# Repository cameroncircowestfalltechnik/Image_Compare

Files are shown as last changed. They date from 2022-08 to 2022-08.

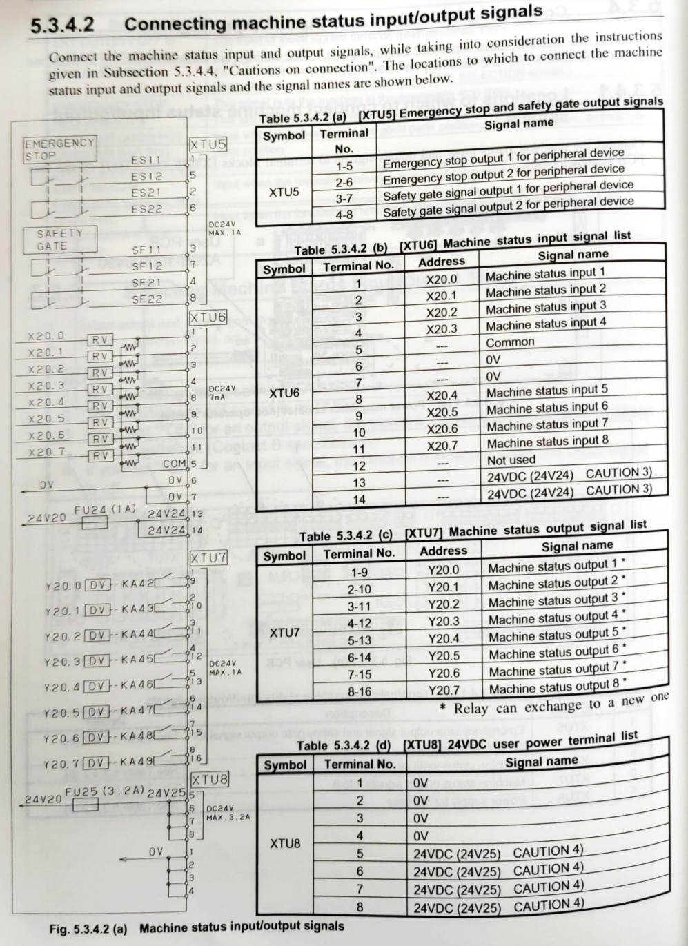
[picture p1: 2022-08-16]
Documentation/Wiring Terminals.png

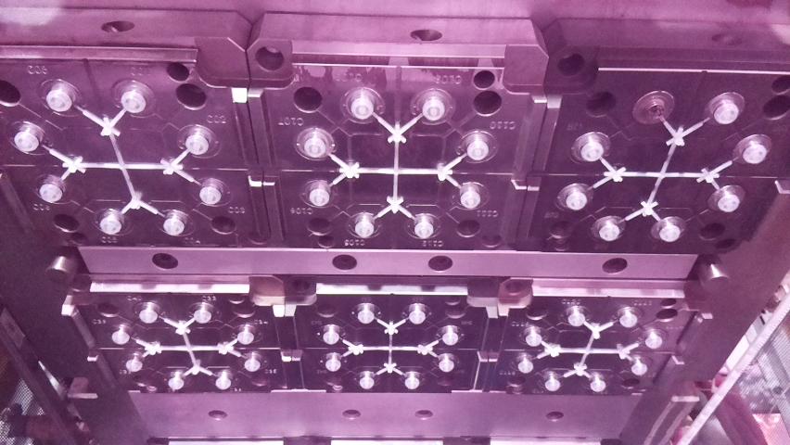
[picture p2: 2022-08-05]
Main/comparison_images/compare_full_ctrl.jpg

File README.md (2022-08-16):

# Main.py is currently the most up to date version!
# Image_Compare
This is yet another look at the current state of the project. Below I will go over each file in the repo. This time around the system contains two Raspberry Pi's a client attached to the machine that is able to operate independently and a server that is currently just used for data archival.

# Scripts
### Main.py
This is the main program of the current config and lives on the client. It has two "daughter" programs that allow it to transmit to the server and restart properly but we'll go through those a little later.  
The general flow of the program is the following:  
-Startup and pull settings from config txt and write to the startup log  
-Calculate the max possible score to be able to classify misfires  
-startup the camera and wait for the input signals  
  -On mold open it collects an image of a mold full of parts then processes/analyzes it  
  -After eject fire it waits a moment and then takes a picture of the empty mold then processes/analyzes it  
  -Interprets the processing output and decides to either throw the alarm or not  
-Simultaneously it maintins a GUI capable of the following:  
  -Changing the camera/analysis settings behind a password protected window  
  -Save the settings to the config file  
  -Genearate an image mask to specify regions to check for discrepencies  
  -See help on how to operate the system  
  -Grant alarm access  
  -Transmit files  
  -Reset the password  
  -Open/close a touchscreen keyboard ([See this tutorial for setup](https://ozzmaker.com/virtual-keyboard-for-the-raspberry-pi/))  
  -View and reset both control images  
 I recommend going through the code line by line for exact detail as I commented just about every line

### Dev_old.py
This is a depreceated version of Main that moved most of the settings buttons to the main GUI page, this made debugging much easier as they buttons were not on their own password protected window.  

### Main_B.py
This is a variant of the main program designed to be deployed on a different setup. The main changes are that it is designed to maintaina single image, used larger images and process more efficiently. This is described in detail below:  
-Only processes masked areas at the cost of forcing masked area to be rectangular  
-Uses opencv contour detection to detect the areas defined by masking tool  
-Captures 1920x1080 images by default and then downscales them in all the GUI elements in order to display properly  

### Main_Startup.py
 This program allows the main script to restart itself. I encountered an issue where the program could start a new iteration of itself but would never close the old one. This would lead to a memory leak. As such this program is designed to attempt to close the main program and then launches it. Finally, the main program attempts to stop this program on its startup. This program is intended to be run on client startup.  

### Main_Transmit.py
This program is designed to transmit the the log files and output images to the server via SCP. From there it deletes the output images to save storage on the client. Additionally, this script is designed to wait for a receipt from the server or will timeout after a designated time as to designate to the operator whether or not files have been recieved by the server. This can also accept a couple arguments. Argument one is an optional argument to override the default server ip. Argument two is an optional argument to make the transmission status display via popups. Seeing as this script will run autonomously via scheduling but must also be able to run via user input it is important to give the user feedback with popups but not spam the screen with popups when run automatically. This script lives on the client.   

### Main_Recieve.py
This program is hosted on the server and checks for the reception of the client receipt. Upon its arrival it checks the receipt for the incoming image folder size as well as client IP. From there it waits for the image folder it is recieveing to be the same size as designated by the receipt. Once the whole folder is transfered, this script sends the server receipt. From here the script moves the files to the archive for the current day of the week. The archive in this case is a usb flash drive that can simply de disconnected to view data. Additionally if the usb drive is not foubd it will backup locally. This program is intended to be run on startup of the server.  

### Wiring_Check.py  
This program is meant to check the wiring of the relay and test the I/O. It presents a window that allows you to send the alarm and reset signals and displays the mold open and ejector fire signals. Additionally it writes the input signals to the termianl with a timestamp for more detail.  

# Files   
### server_receipt.csv
This is the receipt the server sends to the client. It has no contents and more or less acts as a way for the transmit script to check for a file sent from the server. This could be a good way for the server to send back some info similar to the client receipt discussed below.  
### start.desktop
I followed [this tutorial](https://learn.sparkfun.com/tutorials/how-to-run-a-raspberry-pi-program-on-startup/method-2-autostart) on setting up programs to run on boot with a GUI. Currently, in my system, its destination folder is /home/pi/.config/autostart. On the pi the file is called "prog" not "start" but this is likely a difference in raspbian vs windows choosing how to display as "prog" is defined in the contents of the file. In the current setup in just launches predeployment_copy.py but in the main deployment will run Main_Emulated_Startup.py. A similar setup of this is used to run Main_Recieve.py on startup of the server.  
### run.desktop  
I followed [this tutorial](https://www.hackster.io/kamal-khan/desktop-shortcut-for-python-script-on-raspberry-pi-fd1c63) on setting up executables for programs. This is meant to live on the desktop screen and acts as a shortcut to startup Main.py if operators accidentally close the program. I recommend enabling "Don't ask options on launch executable file" under Edit->Prefrences->General in the raspbian file explorer to execute this more seamlessly.  

# Main folder
This is a sample of the filesystem client programs use. It shows some samples of outputs as well as demonstrates the layout of the file system.  
### client_receipt.csv
This is the csv file sent by Main_Emulated_Transmit.py to the server to tell it the file size and client ip. Additionally the server checks for this file to confirm it is recieveing files. Line one contains the image folder size in bytes, line two contains the client ip.  
###  log.csv
This is the main log that tracks the decision making of Main.py every time it does processing. This formatted as to be self explanitory. As you can see logs contain the timestamp which doubles as the output image title, the score the image recieved, and whether or not it set off the alarm.  
### log_template.csv  
This is a copy of the log but with no data present. It is used by transmit to wipe the log file. This is done by copying this file over the log and naming it log.  
### startup_log.csv
This log is written to once on every startup, it tracks the startup time and settings upon startup. This one is also formatted to it should be pretty self explanitory when viewed in github.  
### config.txt
This is a sample of my current config file. It stores the following in this order, password, ISO, shutter speed, camera mode, image width, image height, image rotation, image detection threshold, sensitivity, mold open delay, ejector fire delay, machine name, and alarm access. 
### menu_image.jpg
This is a sample image that is used as the first image to be displayed when the client programs are launched. It stands as a placeholder until the program processes and displays a new image.  
### mask_preview.jpg  
This an image of the full control with the mask overlayed on top of it. It is intended to be part of the archive and allows the user to have a visual representation fo exactly what parts of the mold are being examined at the time of archival. This image is updated on startup and everytime a new mask is generated.  
### images folder
This is where the outpput images go to be stored and then sent to the server.  
### comparison_images folder
This is the folder in which the sample and control images are stored while the client programs run as well as the image mask.
### fail folder  
This folder contains a set of images for every failure/time the alarm is triggered. Upon an image not passing it saves the current raw input, the processed output, and the control image it is being compared against. This is intended to gice the user plenty of data for analyzing failed images.  

# archive Folder
This is a sample layout of the archive stored on the server desktop and USB drive. It is meant to be copied to theses locations for easy setup. Ignore/delete the files name placeholder, they are present to force githb to keep the folder.  

# Misc/Common Bugs/Setup
### SCP Setup
When setting up SCP file transfer (especially when scheduled via crontab) it is imprtant that the root user also has the credentials for scp transfer. This can be done by following [this tutorial](https://raspberrypi.stackexchange.com/questions/51877/will-an-automated-scp-script-share-files-between-pis-without-passwords/53214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) and then configuring it to be run by root by following [these instructions](https://raspberrypi.stackexchange.com/a/121742) in which you first generate a keyset, copy them between machines and then copy the keyset to be accessed by root. In a couple cases I had to manually make the /root/.ssh folder first.  
### Crontab Setup
I added the following lines to crontab to autorun some things (to make it run correctly setup with the command "sudo crontab -e".  
I added the following line to the client:  
`00 00 * * * /sbin/shutdown -r now` This restarts the system at midnight everyday.  
`05 00 * * * /usr/bin/python3 /home/pi/Desktop/Main_Transmit.py >> /home/pi/logs/Transmit.log 2>&1` This runs Main_Transmit.py everyday at 12:05 am and writes to a log at the specified location for debugging (this will be removed in final deployment).  
I added the following to the server:  
`00 00 * * * /sbin/shutdown -r now` This restarts the system at midnight everyday.  
`@reboot /usr/bin/python3 /home/pi/Desktop/Main_Recieve.py >> /home/pi/Desktop/log.log 2>&1` This runs the file recieve script on boot
### Documentation
This folder contains important files relating to the documentation of the project.
CAD: This folder contains all CAD files relating to the construction of the project. Everything designed to be 3d printed also has an stl.  
BOM.xlsx: This is a spreadsheet of the bill of materials to completely replicate the system
Setup tutorial.docx: This is a word document describing how to setup the system.
Wiring Diagram.png: This is an illustration of the wiring required to setup the system.

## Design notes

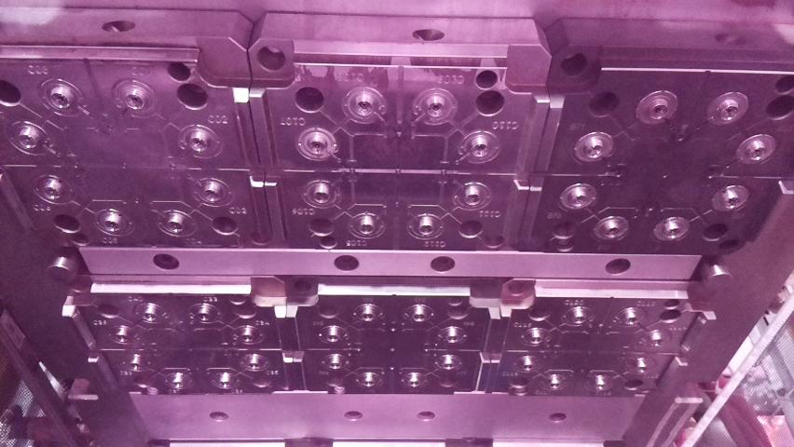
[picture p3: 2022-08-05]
Main/comparison_images/compare_empty_ctrl.jpg

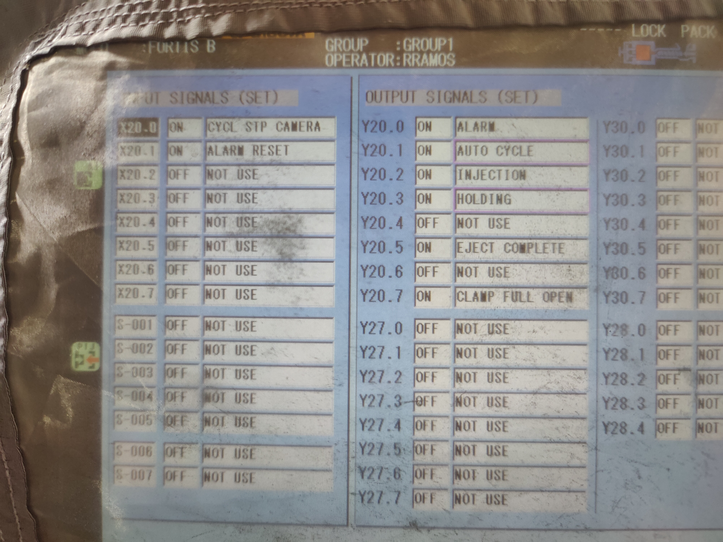
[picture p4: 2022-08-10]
Documentation/Machine IO Config.jpg

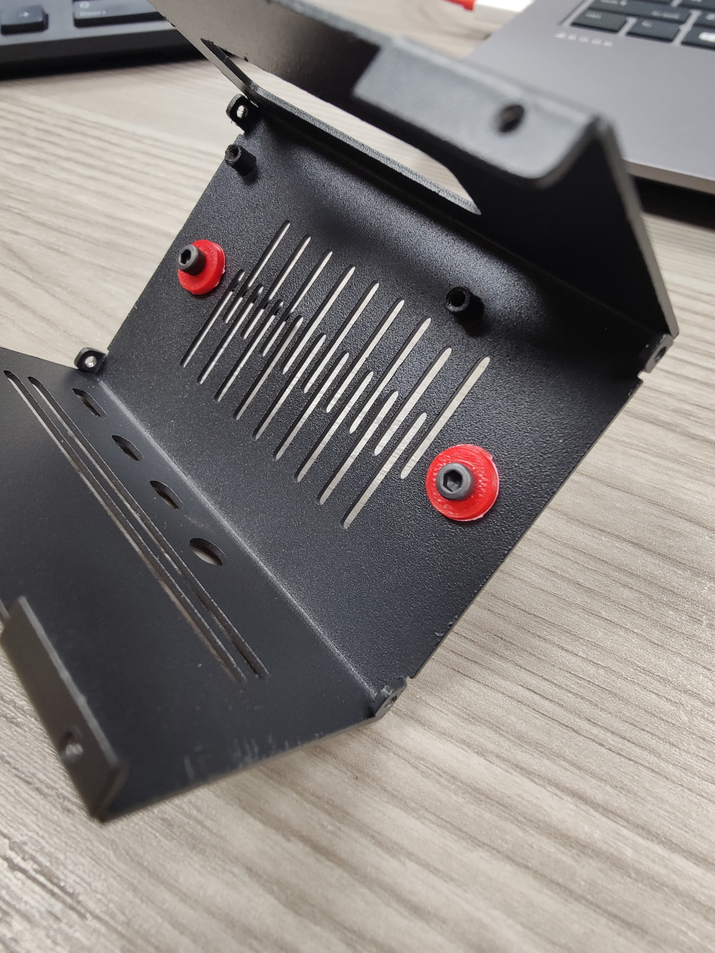
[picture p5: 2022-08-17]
Documentation/Screw Mounting.jpg

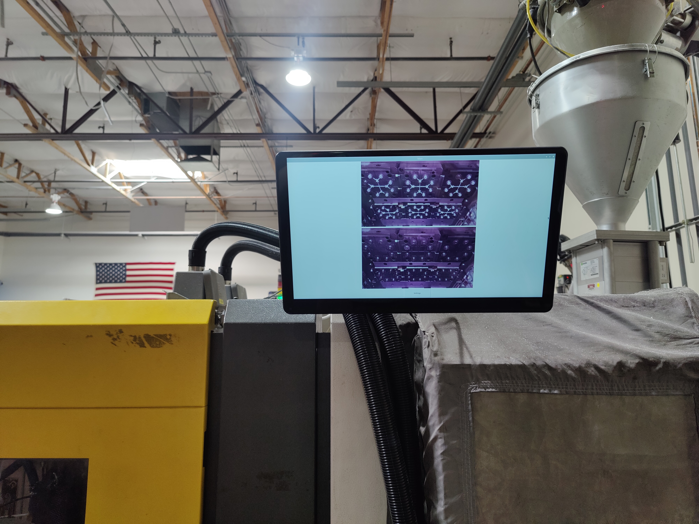
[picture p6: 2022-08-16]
Documentation/TouchScreen Mounting.jpg

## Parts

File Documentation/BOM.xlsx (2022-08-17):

Name | Description | Qty | Unit Cost | Cost | Source | Notes
Client
Raspberry Pi Noir Camera | Captures Images of the mold | 1 | 25.99 | 25.99 | Amazon (https://www.amazon.com/Waveshare-RPi-Camera-V2-Raspebrry/dp/B01FZ7XH6G) | Seeing as we switched to visible spectrum lighting, this is not required to be the NOIR Variant
3Ft. Camera Cable | Connects Camera to the Pi | 1 | 6.99 | 6.99 | Amazon (https://www.amazon.com/Raspberry-Camera-Cable-MazerPi-Ribbon/dp/B09FF6Q5HY)
Raspberry Pi (4Gb) | one client and one server | 1 | 129 | 129 | Amazon (https://www.amazon.com/Raspberry-Model-2019-Quad-Bluetooth/dp/B07TC2BK1X) | In my case the amazon listing attached came with everything from the accesory kit but fans. However, we'll just act under the assumption that this line is for the Pi only.
Pi Case | Contains the Pi, fan, and relay | 1 | 16.99 | 16.99 | Amazon (https://www.amazon.com/GeeekPi-Raspberry-Low-Profile-Horizontal-Included/dp/B085HFTMB1) | I had to manually add holes to mount the fan and relay
Pi Accessories Kit | Contains multiple Items listed below | 1 | 24.99 | 24.99 | Amazon (https://www.amazon.com/GeeekPi-Raspberry-Heatsinks-Preloaded-Included/dp/B0919VJ274)
Plastic Pi Case | Case for the server | 1 | 0 | 0 | Accessory Kit
Micro Sd Card | Storage/Boot Drive for the Pis | 1 | 0 | 0 | Accessory Kit | I highly recommend a card a minimum 10Mb/s write speed
Heat Sinks | Cools the Raspberry pi | 1 | 0 | 0 | Accessory Kit | I used a set from the pi I purchased, as such I only needed to purchase one more
Cooling Fan | Enhances the cooling of the client Pi | 1 | 0 | 0 | Accessory Kit | Seperate Purchase Link (https://www.amazon.com/GeeekPi-Raspberry-30x30x7mm-Brushless-Retroflag/dp/B07C9C99RM)
Micro Hdmi to Hdmi Cable | Connect the display to the client Pi | 1 | 0 | 0 | Accessory Kit
Power Supply | Power the server Pi | 1 | 0 | 0 | Accessory Kit | I used one from the kit an purchased another from amazon
Relay | Control the signal to the alarm | 1 | 5.5 | 5.5 | Amazon (https://www.amazon.com/Tolako-Arduino-Indicator-Channel-Official/dp/B00VRUAHLE) | In the lisiting it states it runs of 5V signals but tooke 3.3V just fine
Touchscreen Display | Display Images and GUI | 1 | 269.99 | 269.99 | Amazon (https://www.amazon.com/Touchscreen-Monitor-15-6-Touch-Black/dp/B0965BDKDN) | Alternate 10" Display (https://www.amazon.com/ELECROW-Raspberry-1920X1080p-Touchscreen-Capacitive/dp/B082HWF2HW)
Display Mount | Allows the display to mount to the machine out of the way of obstructions | 1 | 49.99 | 49.99 | Amazon (https://www.amazon.com/Monitor-Wall-Mount-Adjustable-Bracket/dp/B08B1QK2GJ?asc_contenttype=article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)
M3 x 12mm Screw | Used to mount fan and relay | 4 | 5.95 | 5.95 | Mcmaster | Part #91274A106
M3 Nuts | Used to mount fan and relay | 6 | 2.62 | 2.62 | Mcmaser | Part #90592A085
Relay Spacers | USed to properly mount relay | 2 | 0 | 0 | 3d Printed | CAD (https://github.com/cameroncircowestfalltechnik/Image_Compare/blob/main/Documentation/CAD/Relay%20Spacer.stl)
Female to Female Dupont wires | Connects the relay to the Pi | 3 | 6.98 | 6.98 | Amazon (https://www.amazon.com/EDGELEC-Breadboard-1pin-1pin-Connector-Multicolored/dp/B07GD312VG)
Misc Wires | Connect the Pi to the machine | 1 | 15.99 | 15.99 | Amazon (https://www.amazon.com/West-Penn-Wire-Conductor-Shielded/dp/B08KJR8W4Q) | Any six conductor wire should do. In my case I used 2 runs of 4 wire thermostat wire and attached cupont connectors to the Pi end.
Camera Mounting
Pi Camera Case | Adapts the camera to mount via 1/4-20 screw | 1 | 5.99 | 5.99 | Amazon (https://www.amazon.com/Arducam-Raspberry-Autofocus-Compatible-Official/dp/B09TNG4V55)
Camera Mount | Allows the location and angle of the camera to be easily adjusted | 1 | 19.99 | 19.99 | Amazon (https://www.amazon.com/SmallRig-Adjustable-Articulating-Monitor-Lights-2066/dp/B076KDDBW5)
1/4-20 Thumb Scews (1-1/2 in) | Used for custom camera mount | 1 | 12.78 | 12.78 | Mcmaster | Part #91185A929
1/4-20 Bolt (1-1/2 in) | Used for custom camera mount | 1 | 6.46 | 6.46 | Mcmaster | Part #91268A505
5/8 Aluminum Bar (2ft.) | Used for custom camera mount | 1 | 12.82 | 12.82 | Mcmaster | Part #9008K114
1/4-20 Locknut | Used for custom camera mount | 2 | 6.31 | 6.31 | Mcmaster | Part #95615A120
M4 x 20mm screw | Mount the Pi to the base | 2 | 5.71 | 5.71 | Mcmaster | Part #91274A121
M4 Nut | Mount the Pi to the base | 2 | 3.33 | 3.33 | Mcmaster | Part #90592A090
Mounting Plate | Used for custom camera mount | 1 | 0 | 0 | 3d Printed | CAD (https://github.com/cameroncircowestfalltechnik/Image_Compare/blob/main/Documentation/CAD/Base.stl)
Extension Cord | Provide Power to the Client Pi and display | 1 | 15.99 | 15.99 | Amazon (https://www.amazon.com/Maximm-Rotating-Extension-Outlet-Grounded/dp/B077YT9VTZ) | Can be any sufficiently long cord with two outlets at the end
Cable Conduit | Protect the camera cable | 1 | 18.99 | 18.99 | Amazon (https://www.amazon.com/Electric-Concealer-Management-Organizer-Paintable/dp/B093SS3KWK) | Any conduit at least 0.62" wide should work
Server
Raspberry Pi (4Gb) | one client and one server | 1 | 129 | 129 | Amazon (https://www.amazon.com/Raspberry-Model-2019-Quad-Bluetooth/dp/B07TC2BK1X) | The server should be capable of accepting data from multoiple clients. As such when simply expandinf the system, acquiring another server is redundant.
Pi Accessories Kit | Contains multiple Items listed below | 1 | 24.99 | 24.99 | Amazon (https://www.amazon.com/GeeekPi-Raspberry-Heatsinks-Preloaded-Included/dp/B0919VJ274) | Just like above the amazon listing for the pi came with everything from the accesory kit but fans, but we are assuming the Pi line is for only the pi.
Plastic Pi Case | Case for the server | 1 | 0 | 0 | Accessory Kit
Micro Sd Card | Storage/Boot Drive for the Pis | 1 | 0 | 0 | Accessory Kit | I highly recommend a card a minimum 10Mb/s write speed
Heat Sinks | Cools the Raspberry pi | 1 | 0 | 0 | Accessory Kit | I used a set from the pi I purchased, as such I only needed to purchase one more
Micro Hdmi to Hdmi Cable | Connect the display to the client Pi | 1 | 0 | 0 | Accessory Kit
Power Supply | Power the server Pi | 1 | 0 | 0 | Accessory Kit | I used one from the kit an purchased another from amazon
Usb Stick | Allows the user to easily acces archive | 1 | 8.99 | 8.99 | Amazon (https://www.amazon.com/SanDisk-Cruzer-Glide-Drive-SDCZ60-128G-B35/dp/B007YX9OA8) | I highly recommend a drive that uses at least USB 2.0

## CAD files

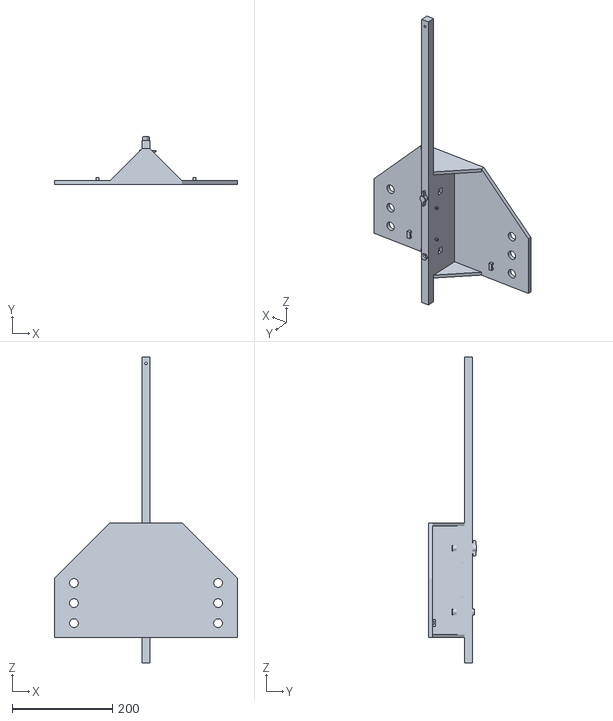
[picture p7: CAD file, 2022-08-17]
Documentation/CAD/Camera Mounting v19.stl
365.1 x 94.9 x 609.6

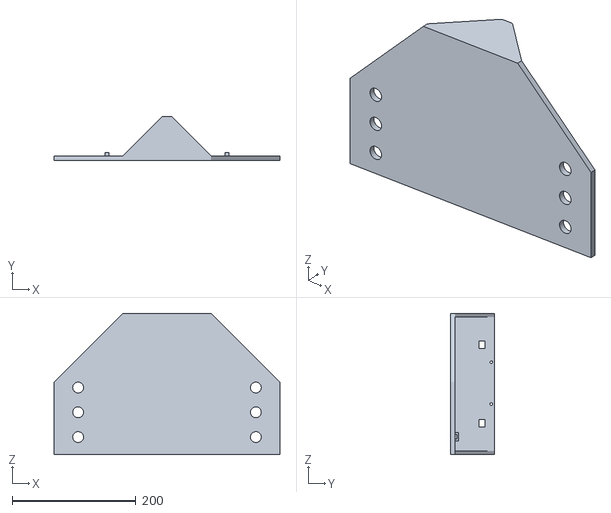
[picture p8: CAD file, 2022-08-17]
Documentation/CAD/Base.stl
365.1 x 71.1 x 228.6

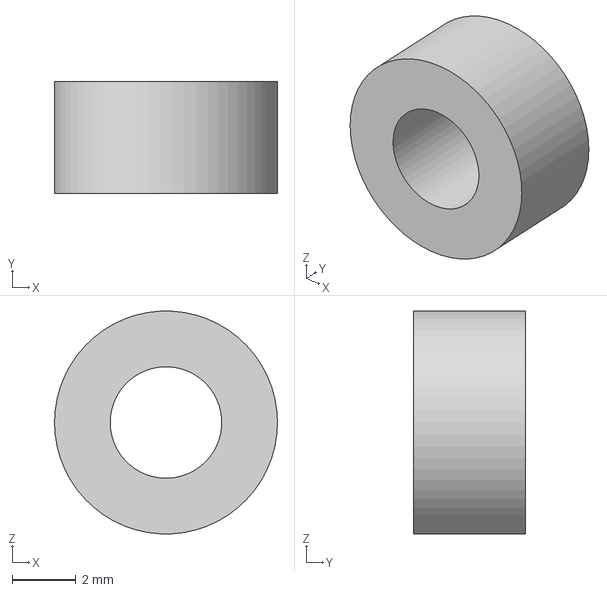
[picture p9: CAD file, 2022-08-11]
Documentation/CAD/Relay Spacer.step
7.00 x 3.50 x 6.99 mm

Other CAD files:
Documentation/CAD/Relay Spacer.stl

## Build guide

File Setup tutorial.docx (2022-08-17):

All commands to type will be specified with gray highlighting

Example

Additionally, all commands are listed in setup commands.txt for ease of copy/pasting. Note: when pasting into a pi terminal use ctrl+shift+v

Client Software Setup

-Option 1 (Fresh install)

1. If the sd card has Raspbian pre-installed skip to step 2B (The BOM listing should facilitate this route). If imaging a blank SD card manually go to 2A.

2A. Follow the Tutorial Here (https://www.raspberrypi.com/documentation/computers/getting-started.html) on how to install an image

Under the gear icon set the following:

-Enable ssh with password authentication

-Username: pi and password: pi

-Configure the wifi password

-Enable locale settings and set to the correct locale

Click save then write, click yes, it will then ask for admin access to write to the drive. wait for the writing to finish and insert the micro sd card into the PI and connect keyboard, mouse, power supply, and display.

Boot the pi and open the menu by clicking the upper left icon. Under preferences open raspberry pi configuration.

-Under display disable screen blanking

-Under interfaces double check that ssh is enabled

-Under localization double check for the correct time zone and keyboard

There is no need to reboot, we will do that at the end

2B. Boot to the Pi with a keyboard, mouse, power supply, and display attached

In the setup tool do the following:

-set the correct country, language, and timezone. Enable the U.S. keyboard

-set the username and password as pi

-connect to the correct Wi-Fi

-update software

-restart

Boot the pi and open the menu by clicking the upper left icon. Under preferences open raspberry pi configuration.

-Under display disable screen blanking

-Under interfaces double check that ssh is enabled

-Under localization double check for the correct time zone and keyboard

3. Open a command console with ctrl+alt+t.

Type: sudo raspi-config

Use arrow keys and enter to navigate. Go to interface options and enable legacy camera support.

Navigate to finish, there is no need to reboot.

4. On a PC go to the Github (https://github.com/cameroncircowestfalltechnik/Image_Compare) and click code then “Download zip”. Save the content of the zip file to the usb stick. Remove the USB stick and plug it into a usb port on the pi.

5. From the usb stick copy the scripts Main.py, Main_Transmit.py, Main_Startup.py and toggle-matchbox-keyboard.sh to the desktop and the folder “Main” to the desktop. Copy “click me to start” and “prog” to desktop.

6. The next few steps install the required libraries, setup the keyboard, configure the main program autostart, and create the file reception server. You can run a script to do these steps automatically by following 6A or you can do each item manually with steps 6B, 7, and 8.

6A. Use the autosetup script: copy “client_setup.sh” from the usb drive to desktop. In a terminal (ctrl+alt+t), run the following commands:

Type: sudo chmod +x /home/pi/Desktop/client_setup.sh

Type: /home/pi/Desktop/client_setup.sh

Wait for the script to finish, you can now start on step 9

6B. Manual setup: Install all the necessary libraries by entering the following commands in a terminal (ctrl+alt+t):

-PIL (Python imaging library): sudo pip install pillow (pre-installed, run to double check install)

-guizero: sudo pip3 install guizero

-picamera: sudo apt-get install python-picamera python3-picamera (pre-installed, run to double check install)

-numpy: sudo apt-get install python3-numpy (pre-installed, run to double check install)

-gpiozero: sudo apt install python3-gpiozero (pre-installed, double check install)

-argparse: pip install argparse

-imagetk: sudo apt-get install python3-pil.imagetk

-Subprocess: pip install subprocess.run

-matchbox keyboard: Do the indented commands below

Type: sudo apt-get install matchbox-keyboard -y

Type: sudo apt-get install libmatchbox1 -y

Type: sudo mv /home/pi/Desktop/toggle-matchbox-keyboard.sh /usr/bin

Type: sudo chmod +x /usr/bin/toggle-matchbox-keyboard.sh

Type: mkdir ~/.matchbox

Type: sudo cp /usr/share/matchbox-keyboard/keyboard-lq1.xml ~/.matchbox/keyboard.xml

Type: sudo chown pi:pi ~/.matchbox/keyboard.xml

Try typing: toggle-matchbox-keyboard.sh

This should make a keyboard with a numpad show up, run the command again to close it

7. Setup main program autostart by running the command “mkdir /home/pi/.config/autostart” and then then running “mv /home/pi/Desktop/start.desktop /home/pi/.config/autostart”.

8. make the file receive folder by running the command “mkdir /home/pi/Desktop/receive”

9. Setup task scheduling by typing “sudo crontab -e” in the terminal and adding the specified lines here (https://github.com/cameroncircowestfalltechnik/Image_Compare)/Written below. This will make the program schedule file transmission and reboots. (use editor 1)

Add the following lines to the bottom:

00 00 * * * /sbin/shutdown -r now

05 00 * * * /usr/bin/python3 /home/pi/Desktop/Main_Transmit.py >> /home/pi/Desktop/Transmit.log 2>&1

Note: the “05” should be different for every client. In this case this transmits at 00:05, space clients at least 30 minutes apart to prevent file reception errors. So the next client would start with “35 00 * * *” and so on

Do ctrl+s and then ctrl+x to save and exit the config window.

10. Configure SCP transfer by following instructions in a command terminal:

Type: ssh-keygen

Press enter at each prompt

Type: ssh-copy-id pi@IP (put the server ip under “IP” (This can be found by running hostname -I on the server))

You may need to press y and then enter

Type yes then enter

Type the server password (“pi”) then enter

Type: sudo chmod 777 /root

Type: sudo cp -r /home/pi/.ssh /root (it may be hard to see but there is a space between “.ssh” and “/root”)

Type: sudo chmod 777 /root/.ssh

11. Open any folder, click edit in the top left, select preferences. Under General check the box that says “Don’t ask options on executable file” This will allow the “click me to start” shortcut to work more seamlessly.

12. shutdown the system to setup hardware (click the pi logo in the top left, click shutdown, then shutdown)

(this can also be done by typing sudo shutdown now)

13. Proceed to client hardware setup

14. The Pi should now boot to the program

15. If this is a new client being added to a setup with a pre-existing server run the following commands on the server:

Type: ssh-copy-id pi@IP (put the new client ip under “IP” (found by mousing over wifi symbol in to right or typing: hostname -I in the terminal ))

Type: sudo cp -r /home/pi/.ssh /root

16. Be sure to configure the settings properly in the program (namely machine name).

-Option 2 (Clone a pre-existing system)

1. Plug pre-existing setup into a display and plug in a keyboard and mouse

2. Connect an empty micro sd card to a USB port. Launch the raspberry pi images by pressing the windows key then opening “SD Card Copier” under “Accessories”. Under “Copy From Device” select the entry with “/dev/mmcblk0” in it, under “Copy To Device” select the attached SD card. It should be the only option.

3. Click start and allow it to copy the contents of the pre-existing client to the new card. This should take quite a while.

4. Remove the SD card and insert it into the new client PI and it will boot with all the contents and configurations of the pre-existing system.

5. Configure SCP transfer by following step 10 above

6. Modify the transmission automation

Type: sudo crontab -e

Modify the following line to be compliant to the note below:

05 00 * * * /usr/bin/python3 /home/pi/Desktop/Main_Transmit.py >> /home/pi/Desktop/Transmit.log 2>&1

Note: the “05” should be different for every client. In this case this transmits at 00:05, space clients at least 30 minutes apart to prevent file reception errors. So the next client would start with “35 00 * * *” and so on

Do ctrl+s and then ctrl+x

7. If this is a new client being added to a setup with a pre-existing server run the following commands on the server:

Type: ssh-copy-id pi@IP (put the new client ip under “IP” (found by mousing over wifi symbol in to right or typing: hostname -I in the terminal ))

Type: sudo cp -r /home/pi/.ssh /root

8. Be sure to configure the settings properly in the program (namely machine name).

Client Hardware Setup

1. Follow this (https://www.youtube.com/watch?v=lAbpDRy-gc0) tutorial on hooking up the camera to a PI

2. Attach heatsinks and mount the PI in the case. Note: place two m3x30 screws in the bottom cross shaped holes of the case before mounting as the pi mounting will prohibit you from placing them. These are the screws that attach the pi to the middle of the camera mount.

3. Replicate the wiring shown here (https://github.com/cameroncircowestfalltechnik/Image_Compare/blob/main/Documentation/Wiring%20Diagram.png) and fan/relay mounting show here (https://github.com/cameroncircowestfalltechnik/Image_Compare/blob/main/Documentation/Relay%20and%20Fan%20Mounting.jpg) (use BOM materials: 4xM3 nuts, 4x M3x12mm screws, and 2xRelay Spacers)(see the note at the end of step 3 for using other machine terminals)

4. Replicate the machine I/O configuration specified below, an example as seen here (https://github.com/cameroncircowestfalltechnik/Image_Compare/blob/main/Documentation/Machine%20IO%20Config.jpg)

The machine I/O panel should have the following entries

-X20.0 ON CYCL STP CAMERA

-Y20.5 ON EJECT COMPLETE

-Y20.7 ON CLAMP FULL OPEN

Note: other Sets of Terminals on the machine can be fond in the operators manual 216 or here (https://github.com/cameroncircowestfalltechnik/Image_Compare/blob/main/Documentation/Wiring%20Terminals.png)

5. Mount the camera and pi in accordance to the CAD model (https://github.com/cameroncircowestfalltechnik/Image_Compare/blob/main/Documentation/CAD/Camera%20Mounting%20v16.stl) in the documentation. The “Camera Mount” from the BOM attaches to the tapped hole on the end of the aluminum bar. Additionally be sure to take advantage of the cable management loops on the base.

6. Mount the system and display as seen in the attached images (https://github.com/cameroncircowestfalltechnik/Image_Compare/blob/main/Documentation/TouchScreen%20Mounting.jpg) using items from the BOM (https://github.com/cameroncircowestfalltechnik/Image_Compare/blob/main/Documentation/BOM.xlsx) (Client Section, namely: Display Mount)

7. Connect the display and client power supply to mains power. I highly recommend doing so sort of cable routing to keep the data and power lines out of the way of the doors and other pinch points. See an example here (https://github.com/cameroncircowestfalltechnik/Image_Compare/blob/main/Documentation/Wire%20Routing.jpg).

8. Connect the display via USB and the micro HDMI to HDMI cables

Server Software Setup

-Option 1 (Fresh Install)

1. If the sd card has Raspbian pre-installed skip to step 2B (The BOM listing should facilitate this route). If imaging a blank SD card manually go to 2A.

2A. Follow the Tutorial Here (https://www.raspberrypi.com/documentation/computers/getting-started.html) on how to install an image

Under the gear icon set the following:

-Enable ssh with password authentication

-Username: pi and password: pi

-Configure the wifi password

-Enable locale settings and set to the correct locale

Click save then write, click yes, it will then ask for admin access to write to the drive. wait for the writing to finish and insert the micro sd card into the PI and connect keyboard, mouse, power supply, and display.

Boot the pi and open the menu by clicking the upper left icon. Under preferences open raspberry pi configuration.

-Under display disable screen blanking

-Under interfaces double check that ssh is enabled

-Under localization double check for the correct time zone and keyboard

There is no need to reboot, we will do that at the end

2B. Boot to the Pi with a keyboard, mouse, power supply, and display attached

In the setup tool do the following:

-set the correct country, language, and timezone. Enable the U.S. keyboard

-set the username and password as pi

-connect to the correct Wi-Fi

-update software

-restart

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

-Under display disable screen blanking

-Under interfaces double check that ssh is enabled

-Under localization double check for the correct time zone and keyboard

3. On a PC go to the Github (https://github.com/cameroncircowestfalltechnik/Image_Compare) and click code then “Download zip”. Save the content of the zip file to the usb stick. Remove the USB stick and plug it into a usb port on the pi.

4. From the usb stick copy the script Main_Recieve.py to the desktop and the folders “archive” and “receive” to the desktop. Go into archive and under each day of the week there should be a placeholder file, delete all of these, they allow the folders to be structured properly in github, but are no longer needed.

5. Install all the necessary libraries by entering the following commands in a terminal (open a terminal with: ctrl+alt+t):

-Subprocess: pip install subprocess.run

6. Setup task scheduling by typing “sudo crontab -e” in the terminal (select editor 1 by typing 1 then pressing enter) and adding the lines:

00 00 * * * /sbin/shutdown -r now

@reboot /usr/bin/python3 /home/pi/Desktop/Main_Recieve.py >> /home/pi/Desktop/log.log 2>&1

Save and exit with ctrl+s then ctrl+x

7. Configure SCP transfer by following instructions in a command terminal:

Type: ssh-keygen

Press enter at each prompt

Repeat the Indented steps for every client before proceeding:

Type: ssh-copy-id pi@IP (put the client under “IP” (found by running hostname -I in a client’s terminal)

You may need to press y and then enter

Type yes then enter

Type the client password (“pi”) then enter

Type: sudo chmod 777 /root

Type: sudo cp -r /home/pi/.ssh /root (it may be hard to see but there is a space between “.ssh” and “/root”)

Type: sudo chmod 777 /root/.ssh

8. Do the server hardware setup below

9. Reboot the system and it should startup automatically. It has no user interface so it will just load to the desktop. You should however see a file called log.log that will indicate the program has at least started up properly

-Option 2 (Clone a pre-existing system)

1. Get to the desktop of a pre-existing system by plugging in a keyboard, mouse, and display.

2. Connect an empty micro sd card to a USB port. Open the image copier by pressing the windows key then opening “SD Card Copier” under “Accessories”. Under “Copy From Device” select the entry with “/dev/mmcblk0” in it, under “Copy To Device” select the attached SD card. It should be the only option remaining.

3. Click start and allow it to copy the contents of the pre-existing client to the new card. This should take quite a while.

4. Remove the SD card and insert it into the new client PI and it will boot with all the contents and configurations of the pre-existing system.

5. Configure SCP transfer by following step 7 from above.

Server Hardware Setup

1. Attach heatsinks and insert into a case.

2. Rename the flash drive to “VISION_SYS” on a PC. Move “archive” to the root folder of the flash drive and delete everything else. Remove the placeholder files in the folder designated to each day, they allow for the github repo to be structured properly but are now no longer needed. This should make it so the only contents of the usb drive are the archive folder. Insert the flash drive into one of the blue USB 2.0 ports for maximum data transfer speed. This usb drive will store all the archived files from the clients or if the drive is missing or not found at the time of file reception they will be saved to the archive folder on the server desktop.

3. Connect to power supply

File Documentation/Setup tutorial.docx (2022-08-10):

Client Software Setup

-Option 1 (Fresh install)

1. On a raspberry Pi with Raspbian OS installed copy the scripts Main.py and Main_Transmit.py to the desktop and the folder “Main” to the desktop. Copy run.desktop to the desktop.

2. Install all the necessary libraries by entering the following commands in a terminal:

-PIL (Python imaging library): sudo pip install pil

-guizero: sudo pip3 install guizero

-picamera: sudo apt-get install python-picamera python3-picamera

-numpy: sudo apt-get install python3-numpy

-gpiozero: sudo apt install python3-gpiozero

-argparse: pip install argparse

-matchbox keyboard: Follow this tutorial(requires additional setup) (https://ozzmaker.com/virtual-keyboard-for-the-raspberry-pi/)

-imagetk: sudo apt-get install python3-pil.imagetk

-Subprocess: pip install subprocess.run

3. Setup task scheduling by typing “sudo crontab -e” in the terminal and adding the lines here (https://github.com/cameroncircowestfalltechnik/Image_Compare). This will make the program schedule file transmission and reboots.

4. Setup main program autostart by running the command “mkdir /home/pi/.config/autostart” and then copying the file start.desktop to “/home/pi/.config/autostart”.

5. make the file receive folder by running the command “mkdir /home/pi/Desktop/receive”

6. Configure SCP transfer by following instructions outlined here (https://github.com/cameroncircowestfalltechnik/Image_Compare). The username is “pi” and the remote server is the ip of the server. The default password is pi

7. Reboot the system and it should startup, be sure to configure the settings properly in the program.

-Option 2 (Clone a pre-existing system)

1. Get to the desktop of a pre-existing system by one of the following options:

-Plug it into a display and plug in a keyboard and mouse

-Connect to the client via PuTTY and run the command “vncserver”. Then connect to the remote desktop via VNC Viewer. The ip should be listed at the end of the vnc server command return or you can type the IP of the client with “:1” added to the end. The username and password are both “pi”.

2. Connect an empty micro sd card to a USB port. Launch the raspberry pi images by pressing the windows key then opening “SD Card Copier” under “Accessories”. Under “Copy From Device” select the entry with “/dev/mmcblk0” in it, under “Copy To Device” select the attached SD card. It should be the only option.

3. Click start and allow it to copy the contents of the pre-existing client to the new card. This should take quite a while.

4. Remove the SD card and insert it into the new client PI and it will boot with all the contents and configurations of the pre-existing system.

5. Configure SCP transfer by following instructions outlined here (https://github.com/cameroncircowestfalltechnik/Image_Compare). The username is “pi” and the remote server is the ip of the server. The default password for is pi

6. Be sure to configure the settings properly in the program.

Client Hardware Setup

1. Follow this (https://thepihut.com/blogs/raspberry-pi-tutorials/16021420-how-to-install-use-the-raspberry-pi-camera) tutorial on hooking up the camera to a PI

2. Replicate the wiring shown here (https://github.com/cameroncircowestfalltechnik/Image_Compare/blob/main/Documentation/Wiring%20Diagram.png)

3. Replicate the machine I/O configuration specified below, an example as seen here (https://github.com/cameroncircowestfalltechnik/Image_Compare/blob/main/Documentation/Machine%20IO%20Config.jpg)

-X20.0 ON CYCL STP CAMERA

-Y20.5 ON EJECT COMPLETE

-Y20.7 ON CLAMP FULL OPEN

4. Mount the system and display as seen in the CAD and attached images using items from the BOM (https://github.com/cameroncircowestfalltechnik/Image_Compare/blob/main/Documentation/BOM.xlsx)

5. Connect the display and client power supply to mains power

Server Software Setup

-Option 1 (Fresh Install)

1. On a raspberry Pi with Raspbian OS installed copy the scripts Main_Recieve.py to the desktop and the file “server_receipt.csv” to a new folder called “receive” on the desktop. Copy the folder “archive” to the desktop (remove the placeholder files in each folder).

2. Install all the necessary libraries by entering the following commands in a terminal:

-Subprocess: pip install subprocess.run

3. Setup task scheduling by typing “sudo crontab -e” in the terminal and adding the lines here (https://github.com/cameroncircowestfalltechnik/Image_Compare). This will make the program schedule reboot and auto starts the program.

4. Configure SCP transfer to the client by following instructions outlined here (https://github.com/cameroncircowestfalltechnik/Image_Compare). The username is “pi” and the remote server is the ip of all clients. (repeat the instructions of the first link for all client IP’s before using the second link). The default password for is “pi”

5. Reboot the system and it should startup automatically. It has no user interface so it will just load to the desktop.

-Option 2 (Clone a pre-existing system)

1. Get to the desktop of a pre-existing system by one of the following options:

-Plug it into a display and plug in a keyboard and mouse

-Connect to the client via PuTTY and run the command “vncserver”. Then connect to the remote desktop via VNC Viewer. The ip should be listed at the end of the vnc server command return or you can type the IP of the server with “:1” added to the end. The username and password are both “pi”.

2. Connect an empty micro sd card to a USB port. Launch the raspberry pi images by pressing the windows key then opening “SD Card Copier” under “Accessories”. Under “Copy From Device” select the entry with “/dev/mmcblk0” in it, under “Copy To Device” select the attached SD card. It should be the only option.

3. Click start and allow it to copy the contents of the pre-existing client to the new card. This should take quite a while.

4. Remove the SD card and insert it into the new client PI and it will boot with all the contents and configurations of the pre-existing system.

5. Configure SCP transfer to the client by following instructions outlined here (https://github.com/cameroncircowestfalltechnik/Image_Compare). The username is “pi” and the remote server is the ip of all clients. (repeat the instructions of the first link for all client IP’s before using the second link). The default password for is “pi”

Server Hardware Setup

1. Insert an empty flash drive to one of the blue USB 2.0 ports and copy the folder “archive” to the drive. (remove the placeholder files in each folder)

2. Connect to power supply

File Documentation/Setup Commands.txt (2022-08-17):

CLIENT:

sudo raspi-config

sudo chmod +x /home/pi/Desktop/client_setup.sh
/home/pi/Desktop/client_setup.sh

sudo pip install pillow
sudo pip3 install guizero
sudo apt-get install python-picamera python3-picamera
sudo apt-get install python3-numpy
sudo apt install python3-gpiozero
pip install argparse
sudo apt-get install python3-pil.imagetk
pip install subprocess.run
sudo apt-get install matchbox-keyboard -y
sudo apt-get install libmatchbox1 -y
sudo mv /home/pi/Desktop/toggle-matchbox-keyboard.sh /usr/bin
sudo chmod +x /usr/bin/toggle-matchbox-keyboard.sh
mkdir ~/.matchbox
sudo cp /usr/share/matchbox-keyboard/keyboard-lq1.xml ~/.matchbox/keyboard.xml
sudo chown pi:pi ~/.matchbox/keyboard.xml
toggle-matchbox-keyboard.sh

mkdir /home/pi/.config/autostart
mv /home/pi/Desktop/start.desktop /home/pi/.config/autostart
mkdir /home/pi/Desktop/receive

sudo crontab -e
00 00 * * * /sbin/shutdown -r now
05 00 * * * /usr/bin/python3 /home/pi/Desktop/Main_Transmit.py >> /home/pi/Desktop/Transmit.log 2>&1

ssh-keygen
ssh-copy-id pi@IP
sudo chmod 777 /root
sudo cp -r /home/pi/.ssh /root
sudo chmod 777 /root/.ssh

sudo shutdown now

SERVER:
pip install subprocess.run

sudo crontab -e
00 00 * * * /sbin/shutdown -r now
@reboot /usr/bin/python3 /home/pi/Desktop/Main_Recieve.py >> /home/pi/Desktop/log.log 2>&1

ssh-keygen
ssh-copy-id pi@IP
sudo chmod 777 /root
sudo cp -r /home/pi/.ssh /root
sudo chmod 777 /root/.ssh

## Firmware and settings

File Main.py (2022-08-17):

# #!/usr/bin/python #uncomment to designate the program as executable
from PIL import Image, ImageOps, ImageChops, ImageEnhance, ImageDraw, ImageFilter, ImageStat
from guizero import App,Text,TextBox,PushButton,Picture,Window,Combo,Box,Drawing
import time
import os
import picamera
from io import BytesIO
import numpy as np
import subprocess
from gpiozero import DigitalInputDevice, DigitalOutputDevice

#setup-----------------------------------------------------------------------------------------------------------------------------------------------------------------------------------------
setup_start = time.time() #start startup timer
print("Program starting. Please wait")
#I/O Setup
mold_open = DigitalInputDevice(4) #assign input pin (GPIO4 or Pin 7) to mold open signal
ejector_fire = DigitalInputDevice(17) #assign input pin (GPIO17 or Pin 11) to ejector fire signal
alarm_pin = DigitalOutputDevice(27) #assign output pin (GPIO27 or pin12) to alarm signal

#file path setup
base_folder = "/home/pi/Desktop/Main"
config_path = base_folder+"/config.txt" #define config file path
comparison_folder = base_folder+"/comparison_images"
output_folder = base_folder+"/output"
log_path = output_folder+"/log.csv" #specify log location
startup_log_path = output_folder+"/startup_log.csv" #specify startup log location
image_folder = output_folder+"/images/"
fail_folder = output_folder+"/fail/"
mask_archive = output_folder+"/mask_archive/"
comp_path = comparison_folder+"/compare_" #specify image file location
menu_image = base_folder+"/menu_image.jpg" #specify location of placeholder menu images

#kill the startup program
try: #attempt the following
    os.system("cd /home/pi/Desktop") #navigate to program location (probably redundant)
    os.system("\n pkill Main_Emulated_Startup.py") #kill the startup script-
except: #upon fail (likely indicating this program was started without the startup prgram being run
    pass #do nothing

#intialize/write some variables
is_first_full, is_first_empty = True,True #intialize the first fire status as true (the first time it fires a signal it will know it is the first time)
good = True #create variable to hold pass/fail status
full_qty, empty_qty = 0,0 #intialize image throwout counters
throwout_qty = 3 #define how many images to throwout upon startup
res_max = (1200, 750) #define the max camera resolution
display_width = 1920 #define display width
display_height = 1080 #define display height
size_max = 5000000000 #set max output folder size (currently 5 GB)
size_status = 1 #create a interger to count how many times the size has been checked and maintain its status
size_check_reset = 10 #define how many times to request a folder check before actually running
fail_count = [0]*2 #counts how many consecutive fails have occured
fail_reset = 10 #specifies how many consectutive fails force a reset
did = [] #create empty list to store mask drawing ids (stores the ids of all drawings on the image)
coords = [] #create empty list to store drawing coordinates
polymode = False #intialize mask drawing mode as polygon mode off
mold_open_old = 1 #intialize the mold open last status
eject_fire_old = 1 #initialize ejector fire last status
full_score = None #intialize full score
full_pass = None #initialize full pass/fail
max_score = None #intialize max score value
x1, y1 = None, None #intialize starting coords of masking tool
tim = time.asctime() #intitizlize current time variable for capture sequence and to save the image mask
tim = tim[:13]+"_"+tim[14:16]+"_"+tim[17:24] #change time text format from hour:minute:second to hour_minute_second (windows filesystems dont like the ":" symbol in filenames)

#define colors for colorizing difference image
black = (0,0,0) #define black pixel rgb value
color = (0,255,0) #define colored pixel rgb value (in this case it's currently green)

#load the control images
full_ctrl = Image.open(comparison_folder+"/compare_full_ctrl.jpg") #load full control from storage
empty_ctrl = Image.open(comparison_folder+"/compare_empty_ctrl.jpg") #load empty control from storage

full_ctrl_candidate = full_ctrl #intialize full control  candidate (this way if the user attempts to reset the control before a candidate is set it doesn' break)
empty_ctrl_candidate = empty_ctrl #intialize empty control candidate

#open the log file
log = open(log_path, "a") #open log csv file in "append mode"

#grab current config settings
with open(config_path,'r') as f: #open the config file
    lines = f.readlines() #write line by line to "lines"
current_password = lines[0].strip() #read line zero as the password
iso = int(lines[1]) #read line 1 as the iso
ss = int(lines[2]) #read line 2 as the shutter speed
cm = lines[3].strip() #read line 3 as the camera mode
res = (int(lines[4]),int(lines[5])) #read lines 4/5 as the camera resolution
rot = int(lines[6]) #read line 6 as the image rotation
thresh = int(lines[7]) #read line 7 as the image detection threshold
sens = float(lines[8].strip()) #read line 8 as the image detection sensitivity
open_delay = float(lines[9].strip()) #read line 9 as open capture delay
eject_delay = float(lines[10].strip()) #read line 10 as the eject capture delay
server_ip = lines[11].strip() #read line 11 as the server IP
name = lines[12].strip() #read line 12 as the machine name
alarm_access = lines[13].strip() #read line 13 as the alarm access status
if alarm_access == "True": #if it read the text "True"
    alarm_access = True #enable alarm access
else: #otherwise
    alarm_access = False #disable alarm access

#The Camera Zone------------------------------------------------------------------------------------------------------------------------------------------------------------------------------------
#capture and process the image
def capture():
    cap_start = time.time() #start image capture timer
    
    #take picture
    stream = BytesIO() #create memory buffer to write images to
    camera.capture(stream, format='jpeg', use_video_port=True) #capture to the buffer
    stream.seek(0) #move to the first image captured
    image = Image.open(stream) #write the image to the PIL object "comp" or comparison
    
    #finish timer
    cap_end = time.time() #stop the image capture time
    cap_time = cap_end - cap_start #calculate elapsed time
    #print('Capture "'+name+'" took: {} seconds'.format(round(cap_time,4))) #display it.
    print('Capture took: {} seconds'.format(round(cap_time,4))) #display it.
    return image
    
def process(name): #possible inputs "full" "empty" "calibrate_max"
    global full_score, full_pass, full_ctrl, empty_ctrl, max_score, tim, full_ctrl_candidate, empty_ctrl_candidate, fail_count
    decision_start = time.time() #start image capture timer
    
    #set the correct control image (ie. we are storing the respective controls as PIL images and we write to the "main" control named "control" based on which image we are capturing)
    if name == "full": #if the arg is "full"
        control = full_ctrl #set the main control to the full control
        comp = capture()
        #comp = Image.open(comparison_folder+"/Edit_full_ctrl.jpg") #manually overwrite image to load
    elif name == "empty": #if the arg is empty
        control = empty_ctrl #set the main control to the empty control
        comp = capture()
        #comp = Image.open(comparison_folder+"/Edit_empty_ctrl.jpg") #manually overwrite image to load
    elif name == "calibrate_max":
        control = full_ctrl #set the main control to the full control
        comp = empty_ctrl
    process_start = time.time() #start image processing timer
        
    #compensate for a difference in brightness
    comp_bw = comp.convert("L") #make black and white copy of comparison image
    control_bw = control.convert("L") #make b&w copy of control
    stat = ImageStat.Stat(comp_bw) #get image stats of b&w comparison
    comp_brightness = stat.mean[0] #average the color (this gives the image brightness)
    stat = ImageStat.Stat(control_bw) #get image stats of b&w control
    control_brightness = stat.mean[0] #average the color (this gives the image brightness)
    
    if comp_brightness > control_brightness: #if comparison image is brighter
        factor = comp_brightness/control_brightness #calculate the brightness factor (will be >1)
        enhancer = ImageEnhance.Brightness(control) #Say we want to change the brightness of the control
        control = enhancer.enhance(factor) #increase the control brightness by our brightness factor
    
    elif comp_brightness < control_brightness: #if the control is brighter
        factor = control_brightness/comp_brightness #calculate the brightness factor (will be >1)
        enhancer = ImageEnhance.Brightness(comp) #Say we want to change the brightness of the comparison image
        comp = enhancer.enhance(factor) #increase the comparison brightness by our brightness factor
    
    #find the difference in the images and apply the image mask
    diff = ImageChops.difference(control, comp) #find difference between images and name it "diff" or difference
    diff = ImageOps.grayscale(diff) #convert the difference to black and white
    diff = ImageChops.multiply(diff,mask) #introduce the masking filter (ie. any pixel location where the masking filter is white, the diff image is allowed to pass. Any pixel location where the masking filter is black, the diff image is turned black )
    #diff = diff.point( lambda p: 255 if p > 255/sens else 0) #turn any point above defined sensitivity white "255" and anything below black "0". Effectively turns grayscale to black and white.
    diff = diff.filter(ImageFilter.GaussianBlur(4)) #blur the image to remove noise
    diff = diff.point( lambda p: 255 if p > 255/sens else 0) #Make all pixels below the defined threshold black and all above white
    
    #analyze the difference and do something with the results
    tot = int(np.sum(np.array(diff)/255)) #convert diff to an array and find the elementwise sum, call it tot for "total". This represents the quantity of pixels that are different
    print('Score: '+str(tot)) #print the "total"
    if (tot > thresh) and (name != "calibrate_max") and (tot < max_score): #if the total number of diffent pixels are more than the defined threshold and we are not doing the max score test do the following:
        #print("Object detected") #say an object was detected
        simulate_alarm()
        good = False #designate as not good/fail
    elif (name == "full") and (tot > max_score): #if the score is higher than the max possible and name is "full"
        print("Misfire!") #say it is a misfire
        good = True #dont set off the alarm
        name = "full misfire" #declate it as a full misfire
    elif (name == "empty") and (tot > max_score): #if the score is higher than the max possible and name is "empty"
        print("Misfire!") #say it is a misfire
        good = True #dont set off the alarm
        name = "empty misfire" #declate it as an empty misfire
    else: #otherwise do the following:
        #print("No object detected") #say an object was not detected
        good = True #designate as good/pass
        #reset_alarm()
            
    process_end = time.time() #stop the timer
    process_time = process_end - process_start #calculate elapsed time since processing start
    #print('Process time: {} seconds'.format(process_time)) #display the image processing time
    decision_time = process_end - decision_start #calculate elapsed time  since decision start
    print('Decision Time: {} seconds'.format(round(decision_time,4))) #display the decision making time

    #generate the output image
    diff = ImageOps.colorize(diff, black, color, blackpoint=0, whitepoint=255, midpoint=127) #convert black and white differenc image to black and color for more contrast when displaying
    enhancer = ImageEnhance.Brightness(comp) #specify that we want to adjust the brightness of comp
    candidate = comp #save the comparison image to as a generic candidate for use later
    comp = enhancer.enhance(0.75) #decrease the brightness of comp by 25% for more contrast when displaying
    result = ImageChops.add(diff,comp) #overlay difference ontop of comp and call it result
    
    #rotate image if needed (if camera is mounted sideways or upsidedown)
    result = result.rotate(rot)
    
    if name == "full": #if the name is "full"
        tim = time.asctime() #grab current time as to match log name and file name
        tim = tim[:13]+"_"+tim[14:16]+"_"+tim[17:24] #change time text format from hour:minute:second to hour_minute_second (windows filesystems dont like the ":" symbol in filenames)
        pic_full.image = result #send results to the picture widget on the main page
        #save output to add to log in a moment
        full_score = tot #save the score
        full_pass = good #save the pass/fail
        full_ctrl_candidate = candidate #update the current control candidate (basically copy the image so that it can write over the current control if desired
        fail_index = 1
    elif name == "empty":
        pic_empty.image = result #send results to the picture widget on the main page
        empty_ctrl_candidate = candidate #update the current control candidate   
        #write the the data from empty and close to a line in the log (run at the end of ejector fire as that will ALWAYS happen after mold open)
        log.write(tim+","+str(full_score)+","+str(full_pass)+","+str(tot)+","+str(good)+"\n") #write time, score, and pass/fail to log
        log.flush()#save it
        fail_index = 0
    elif name == "calibrate_max": #if we are running a full test (compare full image to empty to calculate the highest possible score. anything above this score is a mistimed image
        max_score = int(0.6*tot) #update the internal max score (multiply by 0.9 so that values that are close can still trigger as misfire)
        print("Max Score: "+str(max_score)) #print the highest possible score
        return #leave the function
    elif name == "empty misfire": #if the current capture is an empty misfire
        pic_empty.image = result #refresh the main page image
        empty_ctrl_candidate = candidate #update the current control candidate anyway, we may need to set this as the new control anyway
        return #leave the function
    elif name == "full misfire": #if the current capture is a sull misfire
        pic_full.image = result #refresh the main page image
        full_ctrl_candidate = candidate #update the current control candidate anyway, we may need to set this as the new control anyway
        return #leave the function
    
    #the code should only be able to execute the following if "name" is full or empty
    if check_size(output_folder): #if the image folder enough space
        result.save(image_folder+tim+"_"+name+".jpg") #save results as a jpg with the current date and time
        folder_has_space = True
    else:
        print("output folder full, not saving image")
        folder_has_space = False            
    if good == True: #if the image passed
        fail_count[fail_index] = 0 #reset the fail counter
        set_control(name) #reset the control
        app.bg = "light grey" #reset the background color
    else: #if the image failed
        if folder_has_space == True: #if the image folder enough space
            control.save(fail_folder+tim+"_"+name+"_ctrl.jpg") #save the control to the fail folder
            candidate.save(fail_folder+tim+"_"+name+"_raw.jpg") #save the raw image to the fail folder
            result.save(fail_folder+tim+"_"+name+".jpg") #save a copy of the results to the fail folder
        fail_count[fail_index] = fail_count[fail_index]+1 #iterate the fail count for the current index
        if fail_count[fail_index] > fail_reset: #if the fail count of the current index exceeds the limit
            set_control(name) #reset the control images
            log.write(tim+",Reset,Reset,Reset,Reset\n") #describe the event in the log
            print("Found "+str(fail_reset)+" consecutive fails, assuming reset error, resetting control")
            
#Password Functions---------------------------------------------------------------------------------------------------------------------------------------
def request_settings(): #define code to request the openeing of the settings page
    keyboard("open") #open the keyboard
    pass_win.show() #show the password window
    pass_input.focus() #focus on the password window (user will not need to click on textbox to type password, they can just start typing)

def check_pass(): #define code to check of the password entered is correct
    password = pass_input.value
    if password == None: #if nothing is put in
        pass #do nothing, window closes
    elif password == current_password: #if the password is correct
        print("password correct!") #report into terminal
        pass_win.hide() #conceal the password window
        set_win.show() #make settings window visible
        pass_input.value = "" #clear the password entry box
        keyboard("close") #close the keyboard
    else: #if the password is incorrect
        pass_win.error("Warning", "Wrong Password") #create a new popup stating wrong password
        pass_input.value = "" #clear the password entry box
        
def cancel_pass(): #define what to do when password cancel button or window close is pressed
    pass_win.hide() #hide the password window
    keyboard("close") #close the keyboard
    pass_input.value = "" #clear the password entry box
    
#Button Functions-------------------------------------------------------------------------------------------------------------------------------------------------------------------------------------
def full_ctrl_focus(): #define code to open/focus the full control window
    full_preview.hide() #hide the window (if already hidden nothing will happen)
    full_preview.show() #show the window (this also brings it to the top)

def empty_ctrl_focus(): #define code to open/focus the empty control window
    empty_preview.hide() #hide the window (if already hidden nothing will happen)
    empty_preview.show() #show the window (this also brings it to the top)
    
def reset_alarm(): #define code to reset the alarm
    print("Alarm Reset") #placeholder: print text
    app.bg = "light grey"
    
def simulate_alarm(): #define the code to simulate the alarm
    app.bg = 'tomato' #set app color to red
    if alarm_access:alarm_pin.blink(on_time=0.1,n=1) #if alarm access is enabled make the alarm line "blink" for 0.1s once

def close_settings(): #define code to close the settings window
    sett_close = set_win.yesno("Restart?", "Restart program to send camera new settings? (Required for camera setting changes)") #create popup to ask if user wants to restart to push new settings to camera
    keyboard("close") #close the keyboard
    if sett_close == True: #if the answer is yes
        restart() #restart the program (maybe just migrate this out of a function if this is the only refrence)
    else: #otherwise (if the window is closed or no is selected)
        set_win.hide() #conceal the settings window
        
def camera_preview(): #define code to preview camera view
    camera.start_preview() #start the preview
    time.sleep(10) #wait 10 seconds
    camera.stop_preview() #close the preview
    
#Value Change Functions-------------------------------------------------------------------------------------------------------------------------------------------------------------------------
def change_iso(): #define code to change the iso
    new_iso = iso_input.value #write the input to a variable, "new_iso"
    numeric = new_iso.isnumeric() #check if the input is a number
    if new_iso == None: #if nothing is input
        pass #do nothing
    elif numeric == True: #if the input is numeric do the following
        print("Setting ISO to:"+str(new_iso)) #print to terminal
        iso = int(new_iso) #write over the old value with the new one
        config_write(1,iso) #save to config file
        iso_curr_text.value = "Current ISO: "+str(iso) #update the settings page text
        iso_input.value = "" #clear the textbox
    else: #if the input is not a number
        set_win.error("Warning", "invalid input, not saving") #create a popup error
        
def change_ss(): #define code to change the shutter speed (operates identical to change_iso, see that for line by line)
    new_ss = ss_input.value
    numeric = new_ss.isnumeric()
    if new_ss == None:
        pass
    elif numeric == True:
        print("Setting Shutter Speed to:"+str(new_ss))
        ss = int(new_ss)
        config_write(2,ss) #save to config file
        ss_curr_text.value = "Current Shutter Speed: "+str(ss)
        ss_input.value = "" #clear the textbox
    else:
        set_win.error("Warning", "invalid input, not saving")
        
def change_cm(): #define code to change camera mode
    cm = cm_combo.value #write the input to the camera mode variable
    config_write(3,cm) #save to config file
    print("Setting Camera Mode to:"+cm) #print to terminal
    cm_curr_text.value = "Current Camera Mode: "+cm #update settings page text
    
def change_rot(): #define code to change the image rotation (operates identical to change_iso, see that for line by line)
    new_rot = rot_input.value
    numeric = new_rot.isnumeric()
    if new_rot == None:
        pass
    elif numeric == True:
        print("Setting Image Rotation to:"+str(new_rot))
        rot = int(new_rot)
        config_write(6,rot) #save to config file
        rot_curr_text.value = "Current Image Rotation: "+str(rot)
        rot_input.value = "" #clear the textbox
    else:
        set_win.error("Warning", "invalid input, not saving")
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

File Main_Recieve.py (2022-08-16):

import os
from time import sleep
import subprocess
import time
import shutil
import csv

main_folder = "/home/pi/Desktop/recieve"
results_path = main_folder+"/send"
client_receipt_path = main_folder+"/client_receipt.csv" #define the location of the client receipt
server_receipt_path = main_folder+"/server_receipt.csv" #define the location of the server receipt
image_path = results_path+"images/" #define the location of recieved images
usb_path_A = "/media/pi/VISION_SYS/Archive/" #define the location of the usb drive
usb_path_B = "/media/pi/VISION_SYS1/Archive/" #define an alternate possible location of the usb drive

processing_path = "/home/pi/Desktop/processing/" #define location of processing folder
archive_path = "/home/pi/Desktop/archive/" #defifne location of archive folder
server_receipt_dest = main_folder #define where in the client the server receipt should go

size_cap = None #create a container for the max size of the archive in bytes, this will be populated later
external_size_cap = int(57.3*0.9*100000000) #specify external size cap. In this case 57.3 Gb usable space we'll allocate 90 percent and then convert from Gb to bytes 
internal_size_cap = int(5*100000000) #specify internal size cap. In this case 5 Gb then convert from Gb to bytes
#intialize variables
curr_size = 0 #initialize variable to track current image folder size

def find_oldest_dir(path): #define function to provide the name of the oldest folder in the given path
    directories = os.listdir(path) #get the names of all the folders in the given path
    age = [None]*len(directories) #create a blank array with as many entries as there are folders. This will store the creation dates of each folder
    for n in range(len(directories)): #sweep through n from 0 to the folder qty
        age[n] = os.stat(path+"/"+directories[n]).st_ctime #write unix creation time of the folder name at index n to its corresponding age index
    return path+"/"+directories[age.index(min(age))] #return the name of the folder at the index of the lowest age index (ie. give the name of the folder with the lowest unix creation time)

def check_folder_size(path): #define code to get the size of a folder
    size = 0 #intialize size counter
    for entry in os.scandir(path): #for every entry in the specified path do the following
        if entry.is_file(): #if it is a file
            size = size+os.path.getsize(entry) #add the file size to the total size
        elif entry.is_dir(): #if it is a folder
            size = size+check_folder_size(entry.path) #get the size of the contents of the folder and add them to the total
    return size #return the folder size in bytes

print("Startup: "+time.asctime()) #print startup time for log
#check for files
while True: #forever do the following
    file_exists = os.path.exists(client_receipt_path) #check that client receipt has been recieved
   
   #recieve files
    if file_exists == True: #if it has been recieved
        print("Client Receipt Found!")
        sleep(0.25) #wait a moment for the entire receipt to arrive
        #read info from client receipt
        with open(client_receipt_path, 'r') as r: #open the client receipt in read mode
            reader = csv.reader(r) #create reader
            size = next(reader) #read the first line as the image folder size
            client_ip = next(reader) #read the second line as the client ip
            name = next(reader) #read the third line as the machine name
        name = name[0]
        size = int(size[0]) #convert from single element list to interger
        client_ip = client_ip[0] #convert from single element list to string
        #print("client ip: "+client_ip) #print the client ip
        print("File Size: "+str(size))
        print("Name: "+name)
        print("IP: "+client_ip)
        
        while not os.path.exists(results_path): #do nothing until the file system sees the results folder
            sleep(0.25) #sleep for 0.25s
            #pass
        print("Results found")
        #wait until the recieved image folder size is the same as the client receipt says it should be
        same_data_count = 0 #intialize variable to track whether data transfer is complete
        size_last = None
        #check the size of the recieved folder. If it is the same for 10 consecutive checks (spaced 1 second apart) then the entire set of files must be present
        while same_data_count < 10: #if the data size hasnt changed for less than 10 cycles
            curr_size = check_folder_size(results_path) #chcek the current data size 
            #print(curr_size)
            print("Recieved:"+str(round((curr_size/size)*100,1))+"%") #print the recieved folder size as a percent of expected
            sleep(1) #wait before checking size again to lower resource use
            if curr_size == size_last: #if the data size has not changed
                same_data_count = same_data_count+1 #iterate the same data counter
            else: #if the data size has changed
                same_data_count = 0 #reset the counter to zero
            size_last = curr_size #update last size
        
        #indicate file reception
        print("Transfer Complete") #print file transfer complete
        subprocess.run(["scp",server_receipt_path, "pi@"+client_ip+":"+server_receipt_dest]) #send server reciept
        print("Server Receipt Sent!")
        #save files to desired location
        sleep(1)
        os.remove(client_receipt_path) #delete the client reciept
        tim = time.asctime() #get the current date/time
        day = tim[:3] #extract the day
        numday =  time.localtime() #get the local unix time
        num_day = time.strftime("%d",numday) #extract the day of the month as a number
        title = name+"_"+tim[:3]+"_"+tim[4:7]+"_"+num_day+"_at_"+tim[11:13]+"_"+tim[14:16]+"_"+tim[17:19] #Generate the folder title as the current time/date in form: day_month_num day_at_hout_minute_second
        print("Starting Saving")
        if os.path.exists(usb_path_A): #check if the usb stick path is present (the usb stick is connected and readable)
            save_path = usb_path_A+day #set the output save path as the folder on the usb stick for the current day of the week
            size_cap = external_size_cap #use the external size cap
            print("Saving externally to "+save_path+"/"+title) #print the save location
        elif os.path.exists(usb_path_B): #check if the usb stick path is present at the alternate location(the usb stick is connected and readable)
            save_path = usb_path_B+day #set the output save path as the folder on the usb stick for the current day of the week
            size_cap = external_size_cap #use the external size cap
            print("Saving externally to "+save_path+"/"+title) #print the save location
        else: #otherwise (if the usb stick is not connected)
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

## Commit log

2022-07-15 Fixed Startup log missing password
    [Main_Emulated.py, predeployment_copy.py]
2022-07-15 Fixed missing password
    [startup_log.csv]
2022-07-18 See extended description for added features
    Made windows start as invisible, reduces startup time. Added keyboard and reworked password window to allow changing its position. Closing main window will now stop the program.
    [Main_Emulated.py, predeployment_copy.py]
2022-07-19 See Changes
    -Made transmit accept server ip argument
    -Added server ip to config/settings of main
    -Added Text to help page
    -Renamed keyboard function
    -Enhanced comments on both
    -Updated sample config
    [config.txt]
2022-07-19 Updated to show server ip
    [startup_log.csv]
2022-07-19 Fixed Caps
    [startup_log.csv]
2022-07-22 Add files via upload
    -Changed file naming format to be friendly to copying to cd cards or PCs
    -Fixed file naming to prevent images from writing over eachother
    -Set main window to display both image sets on predeployment copy
    -Added Wiring_Check.py
    [Main_Emulated.py, Wiring_Check.py]
2022-07-22 See Changelog
    -Added two image display
    -Added machine signal emulating buttons
2022-07-27 Fixed image write over bug
    Fixed issue where eject fire image would write over mold open image as they both have the same name. Now the have _1 and _2 suffixes.
    [predeployment_copy.py]
2022-07-27 Optimized image read/write
    Made all the images in "capture" store as PIL objects as opposed to jpgs. This means that the images are not stored on the disk until required(ie. writing a new control or saving the results) Instead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
2022-07-28 Various Changes
    -added full/empty compare to kill misfires.
    -Fixed control image brightness bug.
    -Added mask preview button.
    -Set camera to lock settings after launch.
    -Set Image to blur before running contrast
    [predeployment_copy.py]
2022-08-01 Various Changes
    -Folder size detection will now check a folder and all its subfolders
    -Defective images now sent to designated "fail" folder along with the results output
    -Set program to write over control after a successful cycle. This should counter any drift in the image from slow shifts in ambient light throughout the day
    [predeployment_copy.py]
2022-08-02 Bugfixes and renamed gui containers
    [Main.py]
2022-08-02 Various Fixes
    -Rename settings rows
    -Augment help window text and convert from window to popup
    -Removed unused widget variable naming
    -moved window creation
    [Main.py]
2022-08-03 Modified camera startup and removed image contrast filter
2022-08-03 Multiple Changes
    -Added brightness compensation
    -Converted scores to integers (fixed bug where max score would save as float and then would not load from config)
    -Fixed bug where masking tool would not wipe drawings correctly
    -Fixed bug where updating the control while masking tool is open would wipe drawings
    [Main.py]
2022-08-05 Various Changes
    -Now throws out specified qty on startup
    -Removed brightness logging.
    -Renamed test capture arg to calibrate_max and set to force int
    -Renamed capture to process and made image capture its own function called capture
    -Renamed main_emulated folder to Main
2022-08-05 Changes config/log writing
    -No longer checks to format log
    -No longer writes max score to config
    -Startup log write turned into a function
    -Startup log write done after startup processing but before camera startup
    [Main.py]
2022-08-05 Removed line for max score
    [config.txt]
2022-08-08 Various Changes
    -Removed alarm reset button Digital input.
    -Fixed bug of max score being empty on start.
    -Changed to set controls on startup
    [Main.py]
2022-08-09 Added Machine Naming
    Main:
    -Added Machine name setting to settings page and config
    Transmit
    -Reads name from config.txt and writes to client receipt
    Receive
    -Reads name from client receipt and writes it at the beginning of archive folder name.
    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
2022-08-10 Added machine names column
    [startup_log.csv]
2022-08-10 Added Machine Name Column
    [startup_log.csv]
2022-08-11 Lowered the autogenerated max score coefficient
    The max score generated on startup was too high, so the factor it is multiplied by has been changed from 0.9 to 0.75. It show now more accurately identify misfires.
    [Main.py]
2022-08-12 Fixed file transmission bug
    Transmit:
    -Now renames output to send and then sends send and rebuilds output. This allows it to more seamlessly keep writing to the folder while transmitting.
    Receive:
    -Now looks for send instead of output
    [Main_Recieve.py, Main_Transmit.py]
2022-08-15 Various Changes
    -Renamed the copy of main with debug elements present to Dev_old
    -Uploaded experimental version and named it Main
    -Added fail reset counter to Main, this forces a control reset on 10 consecutive fails of either sample
2022-08-15 Various fixes
    -start was starting wrong program
    -config was missing machine name
    [config.txt]
2022-08-16 Various Fixes and added setup shell scripts
    [Main_Recieve.py, Main_Transmit.py]
2022-08-16 Fixed settings window placement and added keyboard toggle
    [Main.py]
2022-08-16 Added alarm access
    [config.txt]
2022-08-16 Added alarm access column
    [startup_log.csv]
2022-08-17 Fixed camera resolution limiting bug
    [Main.py]
2022-08-17 Added camera preview button
